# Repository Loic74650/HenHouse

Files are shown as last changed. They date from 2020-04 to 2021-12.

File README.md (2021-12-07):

<h2>HenHouse V2.0</h2>
<h3>solar powered smart and automated hen house system with LoRaWan connectivity</h3><br />

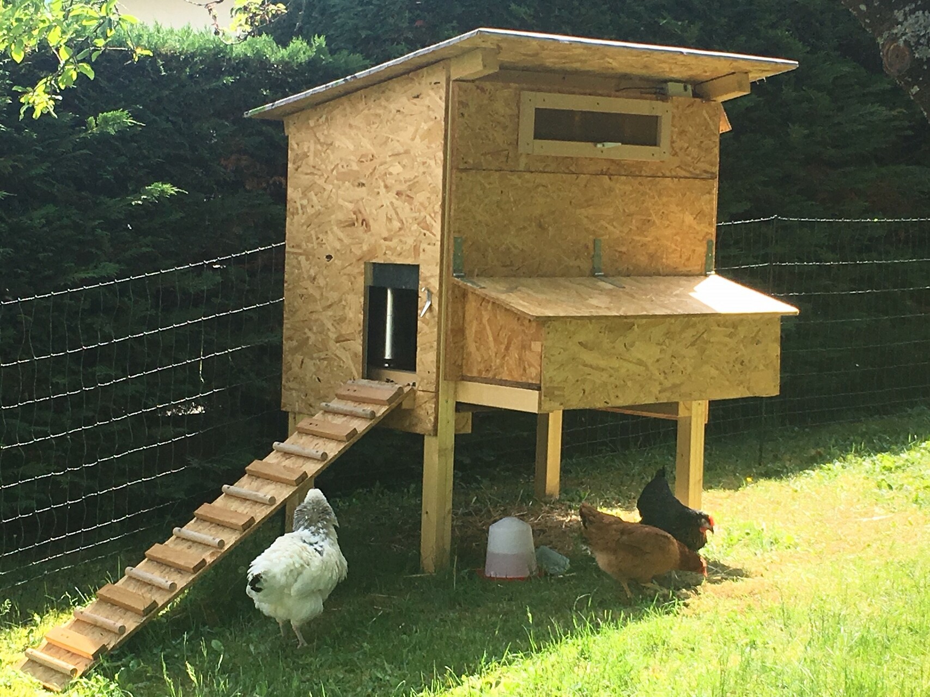
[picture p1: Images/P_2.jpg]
 <br /><br />

<h4>Key features</h4>
<li>Runs on an Adafruit Feather M0 board (ATSAMD21G18 ARM Cortex M0 processor, clocked at 48 MHz and at 3.3V logic) equiped with a LoRa Radio Module</li>
<li>LoraWan connectivity to TTN network based on LMIC fully compliant library</li>
<li>Entrance guillotine-style door is motorized. Two reed end-switches detect the door open/close positions</li>
<li>UP/DOWN interface buttons to manually force door opening/closing</li>
<li>Door automatically opens/closes at sunrise and sunset (as a function of an ambient light threshold, measured via the solar panel voltage output)</li>
<li>When door is moving, a buzzer makes intermitent beeps in order to let the chiken know it is bedtime</li>
<li>Measures the individual temperature of 4 separate nesting boxes (aim is to detect when a new egg was layed) + computes an average</li>
<li>Runs on a 3.7V 4400mAh Lithium Ion Battery Pack and a 6V, 1W solar panel</li>
<li>Goes to deep sleep until UP/DOWN buttons are pressed. 80µA Current consumption in deep sleep mode. </li>
<li>broadcasts over LoraWan every three minutes the systems’ metrics (temperatures, ambient light level, door position, battery level and charging status), received by home automation system in JSON format via MQTT broker</li><br /><br />

In order to broadcast data to the TTN network, you need to register an account as well as the Feather board. <a title="https://learn.adafruit.com/the-things-network-for-feather?view=all" href="https://learn.adafruit.com/the-things-network-for-feather?view=all">Detailed instructions here</a>.<br /><br />

<h4>Hardware</h4>
<li>x1 <a title="https://learn.adafruit.com/adafruit-feather-m0-radio-with-lora-radio-module/downloads" href="https://learn.adafruit.com/adafruit-feather-m0-radio-with-lora-radio-module/downloads">Adafruit Feather M0 LoRa Radio (RFM9x)</a></li>
<li>x1 <a title="https://www.adafruit.com/product/390" href="https://www.adafruit.com/product/390">Solar Lithium Ion/Polymer charger</a></li>
<li>x1 <a title="https://www.sparkfun.com/products/14451" href="https://www.sparkfun.com/products/14451">TB6612FNG</a> motor driver</li>
<li>x1 <a title="https://www.adafruit.com/product/3809" href="https://www.adafruit.com/product/3809">6V 1W Solar Panel</a></li>
<li>x1 <a title="https://www.adafruit.com/product/354" href="https://www.adafruit.com/product/354">Lithium Ion Battery Pack - 3.7V 4400mAh </a></li>
<li>x2 <a title="https://www.adafruit.com/product/375" href="https://www.adafruit.com/product/375">magnetic contact switch (door sensors) </a></li>
<li>x1 <a title="https://fr.banggood.com/DC-3V-6V-DC-1120-Gear-Motor-TT-Motor-for-Arduino-Smart-Car-Robot-DIY-p-1260117.html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" href="https://fr.banggood.com/DC-3V-6V-DC-1120-Gear-Motor-TT-Motor-for-Arduino-Smart-Car-Robot-DIY-p-1260117.html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">motorreductor </a></li>
<li>x1 <a title="https://www.banggood.com/DC-2V-24V-To-5V-28V-2A-Step-Up-Boost-Converter-Power-Supply-Module-Adjustable-Regulator-Board-p-1566600.html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" href="https://www.banggood.com/DC-2V-24V-To-5V-28V-2A-Step-Up-Boost-Converter-Power-Supply-Module-Adjustable-Regulator-Board-p-1566600.html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">DC-DC converter 5V output</a></li>

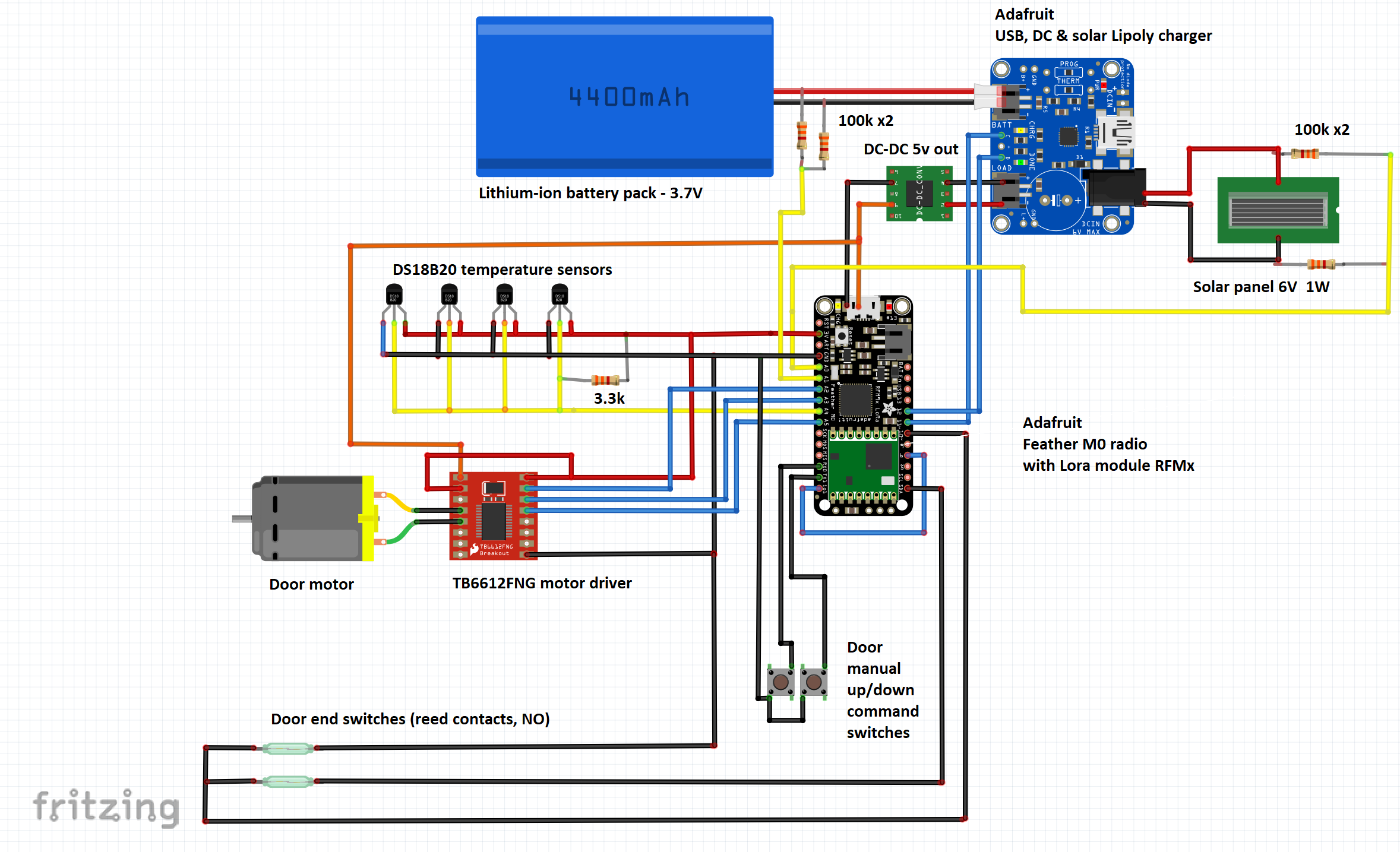
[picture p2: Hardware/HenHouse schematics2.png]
Schematics
 <br /><br />
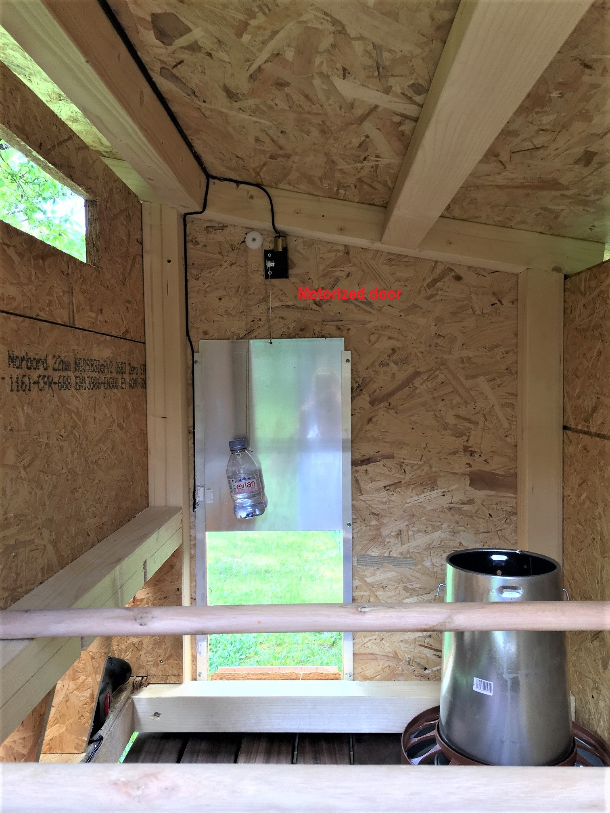
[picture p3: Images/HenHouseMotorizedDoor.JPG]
 <br /><br />
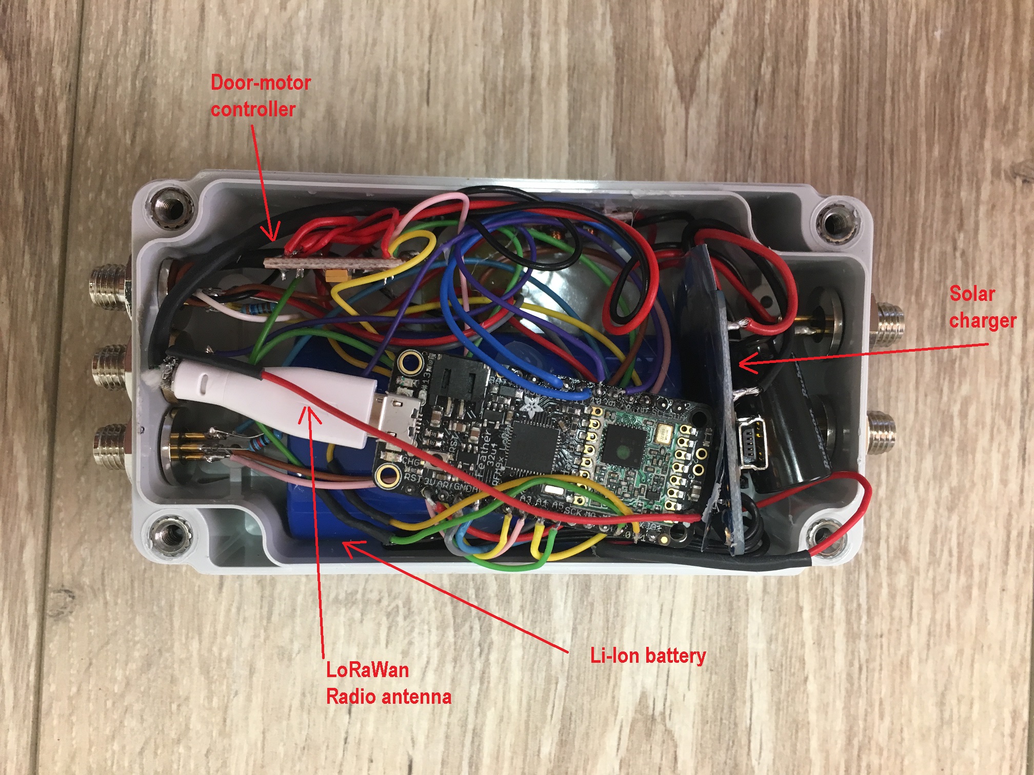
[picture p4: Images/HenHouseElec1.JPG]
 <br /><br />
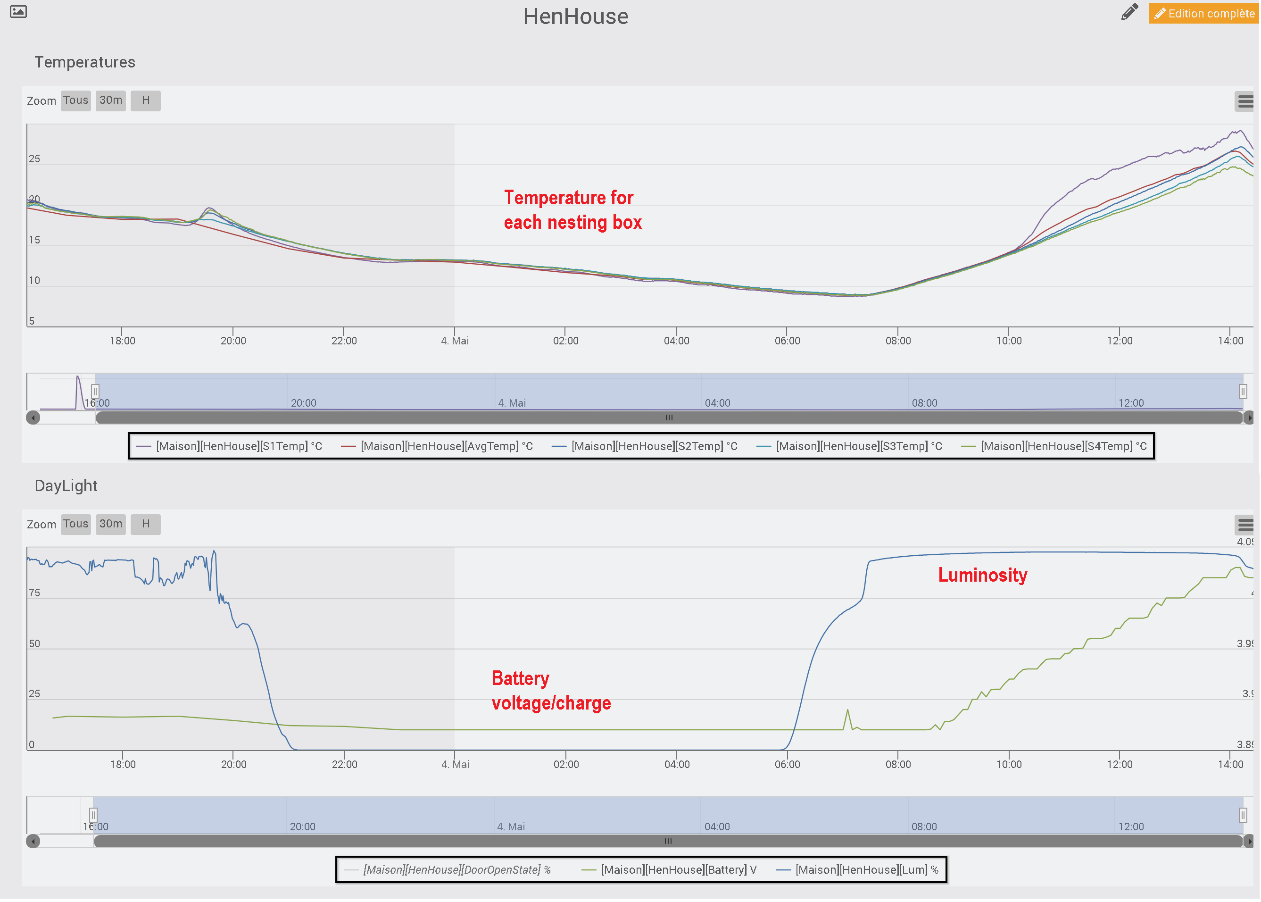
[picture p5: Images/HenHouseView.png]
 <br /><br />

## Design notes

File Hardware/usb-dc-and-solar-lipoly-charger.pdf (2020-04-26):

# USB, DC & Solar Lipoly Charger

Created by lady ada

Last updated on 2018-08-22 03:31:26 PM UTC

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
## Guide Contents

## Guide Contents Overview FAQ

Is this a MPPT tracker?
Why didn't you make this an MPPT?
BUT I HEARD THAT MPPT IS THE BEST!!
OK so how does it work?
What solar panels can I use?
Can I charge with a solar panel on my windowsill?

## Solar Charger Preparation

Installing the Capacitor

## Solar Panel Preparation

Splice or Adapt?

## Voltaic Panels with 1.3mm Connectors Other 6V Solar Panels

Method 1

## If You Have a Pre-2013 Solar Charger Using the Charger

Solar Charging
USB & DC Charging
Indicator LEDs

## Load Sharing

Temperature Monitoring
Adjusting the Max Charge Current

## Adding External LEDs Design Notes

Is this a Max Power Point Tracker (MPPT)? Why a special solar charger?
Solar Optimization!

## Downloads Files Schematic & Fabrication Print

© Adafruit Industries | https://learn.adafruit.com/usb-dc-and-solar-lipoly-charger | Page 2 of 29

## Overview

Make your projects to go green this summer with our specialized USB/Solar Lithium Ion Polymer Battery charger! This charger is a very unique design, perfect for outdoor projects, or DIY iPod chargers. We've spent over a year testing and tinkering with this charger to come up with a plug and play solution to charging batteries with the sun and we're really pleased with what we ended up with.

Easy to use! Pick up any of our many 3.7V/4.2V LiIon batteries (http://www.adafruit.com/category/44) (https://adafru.it/aN5), and a 6V solar
panel (https://adafru.it/aN6). Plug the battery into the BATT port using a 2-pin JST cable and the solar (http://www.adafruit.com/category/67) panel into the DC jack. Put the solar panel outside (and keep the battery out of the sun, it needs to be kept shaded!) to start charging. You can power another project like a Mintyboost at the same time by connecting to the LOAD output port

3.7V/4.2V Lithium Ion or Lithium Polymer battery charger
Charge with 5-6V DC, USB or 6V solar panel!
Too dark out? Use a USB mini-B cable (http://www.adafruit.com/products/260) (http://adafru.it/260) or a 5V DC adapter (http://www.adafruit.com/products/276) (http://adafru.it/276) Automatic charging current tracking for high efficiency use of any wattage solar panel
Use any 6V solar panel (6V seems to work best, 5.5V may work, 5V does not work)
Three color indicator LEDs - Power good, Charging and Done
Low Battery Indicator (fixed at 3.1V) with LED output on (labeled CHRG)
Set for 500mA max charge rate, can be adjusted from 50mA up to 1A by soldering in a resistor
Will always draw the most current possible from a solar cell - up to the max charge rate!
Smart load sharing automatically uses the input power when available, to keep battery from constantly charging/discharging
Temperature monitoring of battery by soldering in a 10K NTC thermistor(http://adafru.it/372) (http://www.adafruit.com/products/372) (not included) -suggested for outdoor projects where the battery may get hot (50°C) or cold (0°C).
© Adafruit Industries | https://learn.adafruit.com/usb-dc-and-solar-lipoly-charger | Page 3 of 29

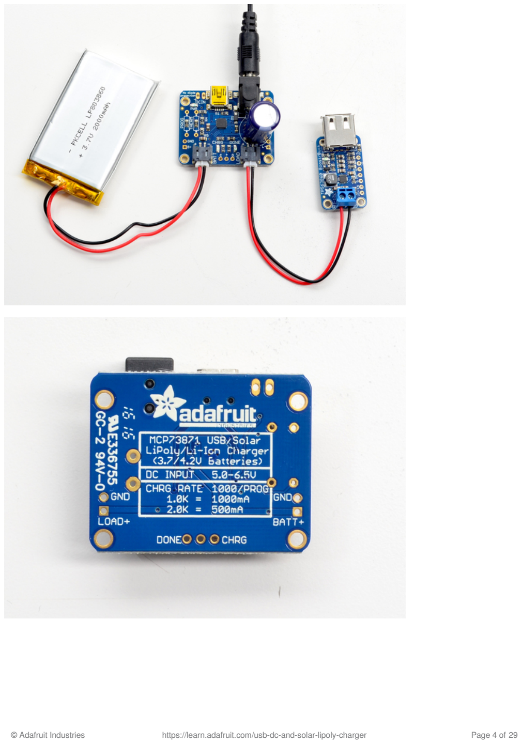
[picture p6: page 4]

© Adafruit Industries | https://learn.adafruit.com/usb-dc-and-solar-lipoly-charger | Page 4 of 29

## FAQ

Is this a MPPT tracker?
This is not a true MPPT tracker, for information on why we did not design it as a true MPPT, read our design notes! (http://learn.adafruit.com/usb-dc-and-solar-lipoly-charger/design-notes)

Why didn't you make this an MPPT?
For low power solar charging of lithium ion's, its not necessarily a better way to charge.For information on why we did not design it as a true MPPT, read our design notes! (http://learn.adafruit.com/usb-dc-and-solar-lipoly-charger/design-notes)

BUT I HEARD THAT MPPT IS THE BEST!!
For large multi-watt solar arrays that are charging lead acid batteries, you will want to get an MPPT charger. For small cells, its not necessarily more efficient. For information on why we did not design it as a true MPPT, read our design notes! (http://learn.adafruit.com/usb-dc-and-solar-lipoly-charger/design-notes)

OK so how does it work?
Good question! For information on how this charger works, read our design notes! (http://learn.adafruit.com/usb-dc-and-solar-lipoly-charger/design-notes)

What solar panels can I use?
Use any rigid, flexible, monocrystal, polycrystal, etc panels with 6V rating (12 'cells') for the best performance

We've tried 5V panels and they don't work. 5.5V panels sometimes work, 6V is really the best!

Can I charge with a solar panel on my windowsill?
The charger will draw as much current as possible, but the efficiency of the panel will be much lower. Solar panels must not have any glass or shade to work efficiently, they must be outside, pointed as best as possible directly at the sun!
© Adafruit Industries | https://learn.adafruit.com/usb-dc-and-solar-lipoly-charger | Page 5 of 29

## Solar Charger Preparation

## Installing the Capacitor

The first thing to do before starting to charge with a solar panel is to install the large filtering capacitor. This capacitor is necessary to stabilize the panel a little, and since we're going to charge with a lot of current, the capacitor needs to be pretty big. There is a spot on the PCB for the capacitor, you can of course install it directly there by soldering the wires of the capacitor into the pads.

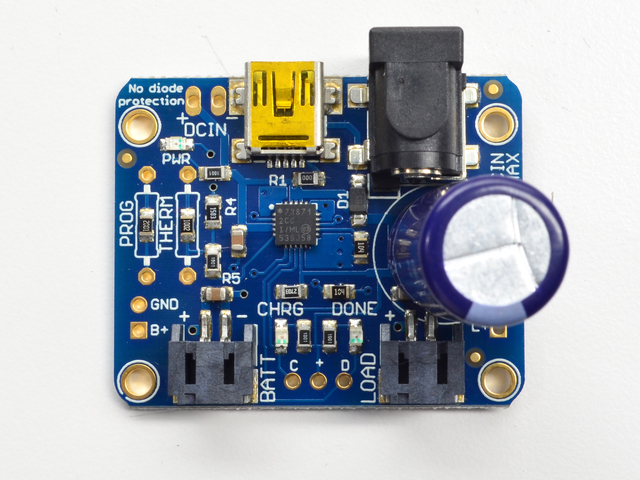
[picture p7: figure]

If you're low on space, you can solder wires to the capacitor and then install it a little farther away. Just remember to use heatshrink to keep the capacitor legs from shorting. If you want you can bend the capacitor over a bit as well, but dont have it touch the hot charging chip (the black square in the middle of the PCB)!

Next you will have to connect up your solar panel. Panels sometimes come 'bare' (no wires), with just wires, or with a connector of some sort. You may need to splice a connector onto the panel to match the 5.5/2.1mm (or 4mm on older charger) DC jack on the adapter.

Make sure to check the polarity of the capacitor, make sure the positive lead of the capacitor goes into the pad marked +!

© Adafruit Industries | https://learn.adafruit.com/usb-dc-and-solar-lipoly-charger | Page 6 of 29

## Solar Panel Preparation

## Splice or Adapt?

The first verison of the solar charger came with a 4mm DC barrel jack on it. On older versions (4mm) it would come with a converter cable.

If you have a newer v2 charger (June 2013+), connect a2.1mm Terminal Block Adapter (http://www.adafruit.com/products/369) (http://adafru.it/369) onto the panel using basic wires, or a 1.3mm to 2.1mm adapter cable (https://www.adafruit.com/products/2788) (http://adafru.it/2788) then plug that into the 2.1mm adapter. This is the fastest method

If you have an older v1 charger, you can use the terminal block method above OR cut the adapter cable in half and splice the 4mm connector onto the panel. The panel will plug right into the board but its more work.

## Voltaic Panels with 1.3mm Connectors

Grab one of our adapter cables, it will let you plug in the solar panel directly (https://www.adafruit.com/products/2788) (http://adafru.it/2788)

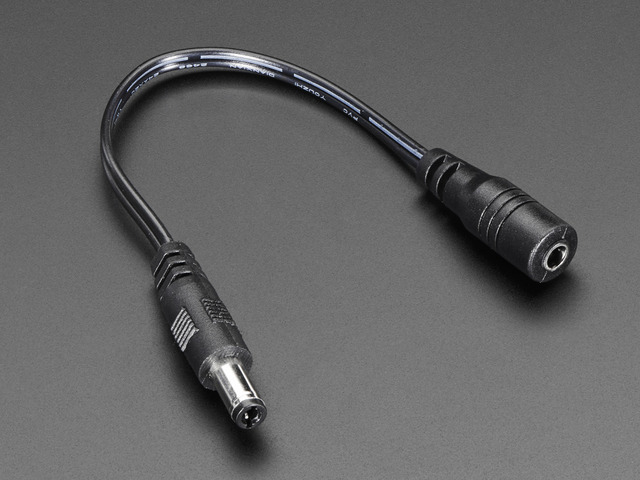
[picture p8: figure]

## Other 6V Solar Panels

If you have a panel with something other than 2.1mm or 1.3mm connector, you'll need to remove any existing connector. Cut off whatever connector is on

© Adafruit Industries | https://learn.adafruit.com/usb-dc-and-solar-lipoly-charger | Page 7 of 29

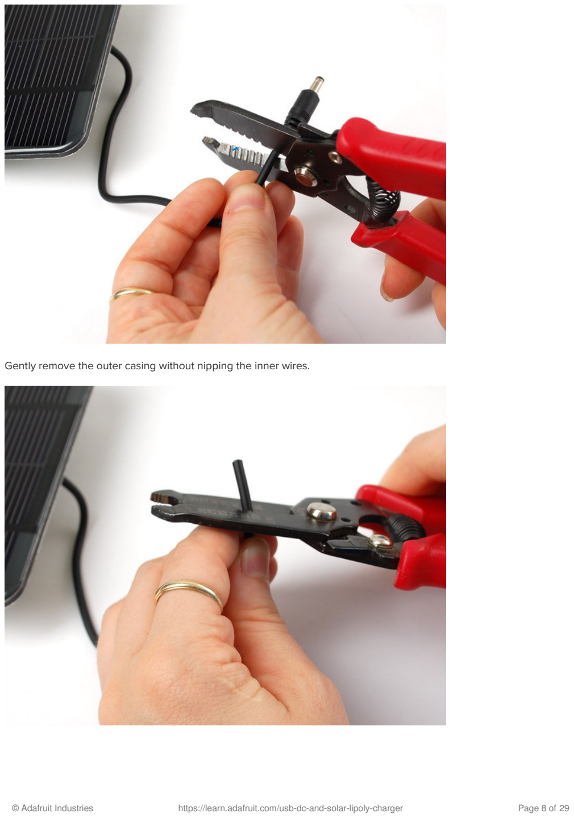
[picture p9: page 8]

Gently remove the outer casing without nipping the inner wires.

© Adafruit Industries | https://learn.adafruit.com/usb-dc-and-solar-lipoly-charger | Page 8 of 29

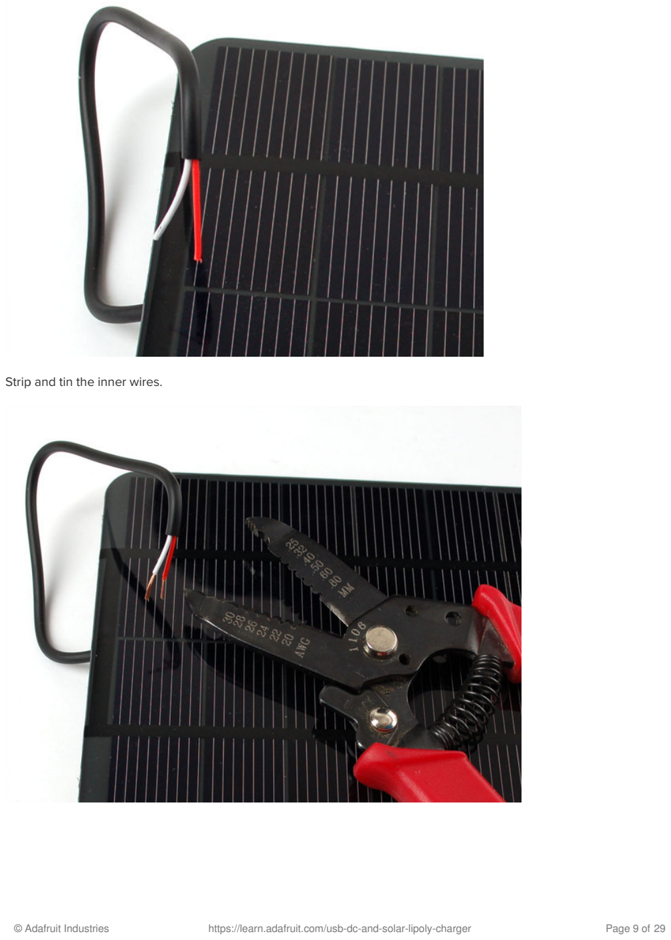
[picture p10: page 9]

Strip and tin the inner wires.

© Adafruit Industries | https://learn.adafruit.com/usb-dc-and-solar-lipoly-charger | Page 9 of 29

## Method 1

For this you'll need a 2.1mm Terminal Block Adapter (http://www.adafruit.com/products/369) (http://adafru.it/369) but its really simple. Just open up the screw terminals, slide the red wire into the + hole and the black wire into the - hole and retighten! Now you can just plug it directly into the charger (or adapter cable).

## If You Have a Pre-2013 Solar Charger

© Adafruit Industries | https://learn.adafruit.com/usb-dc-and-solar-lipoly-charger | Page 10 of 29

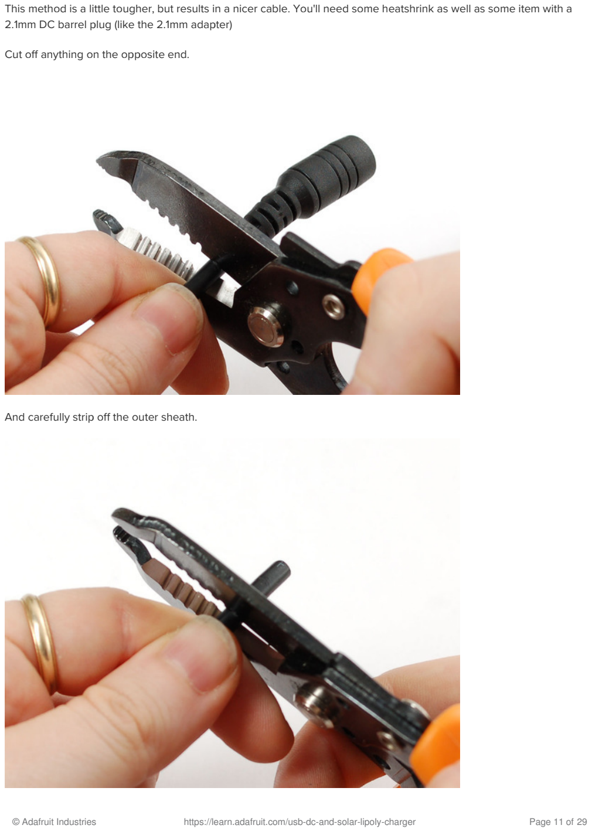
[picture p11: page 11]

This method is a little tougher, but results in a nicer cable. You'll need some heatshrink as well as some item with a 2.1mm DC barrel plug (like the 2.1mm adapter)

Cut off anything on the opposite end.

And carefully strip off the outer sheath.

© Adafruit Industries | https://learn.adafruit.com/usb-dc-and-solar-lipoly-charger | Page 11 of 29

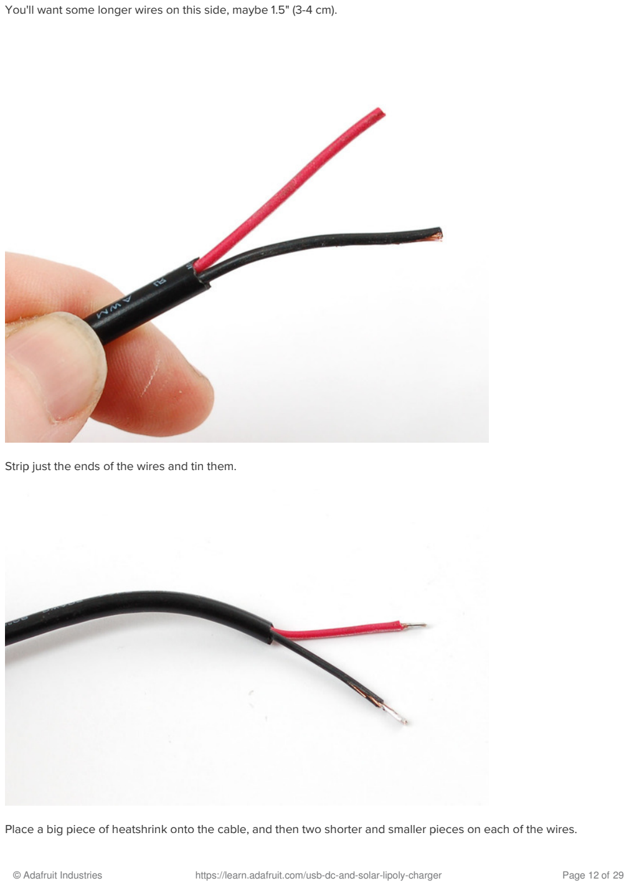
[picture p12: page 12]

You'll want some longer wires on this side, maybe 1.5" (3-4 cm).

Strip just the ends of the wires and tin them.

Place a big piece of heatshrink onto the cable, and then two shorter and smaller pieces on each of the wires.

© Adafruit Industries | https://learn.adafruit.com/usb-dc-and-solar-lipoly-charger | Page 12 of 29

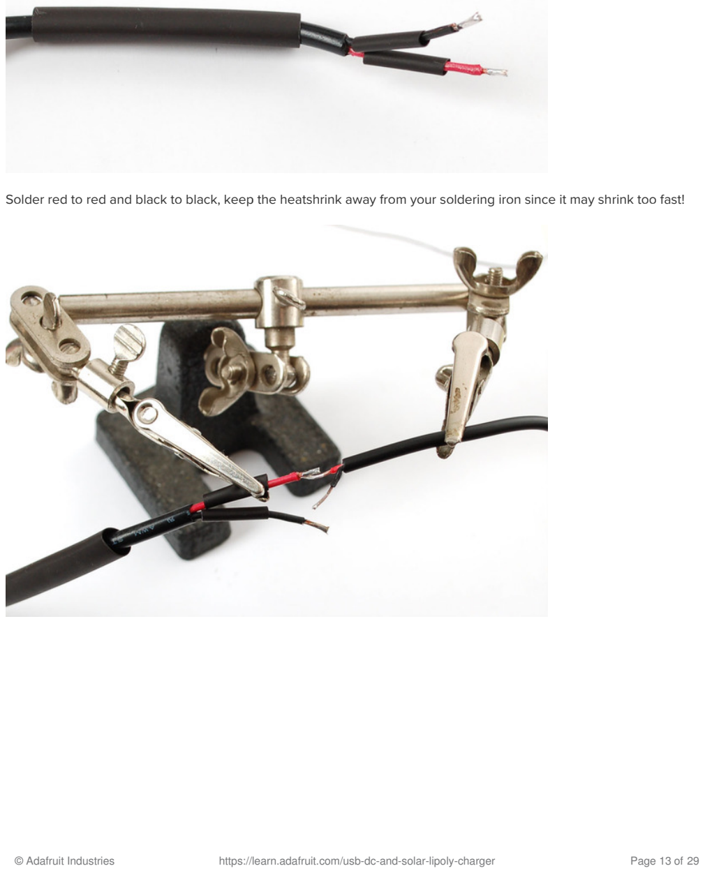
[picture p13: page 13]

Solder red to red and black to black, keep the heatshrink away from your soldering iron since it may shrink too fast!

© Adafruit Industries | https://learn.adafruit.com/usb-dc-and-solar-lipoly-charger | Page 13 of 29

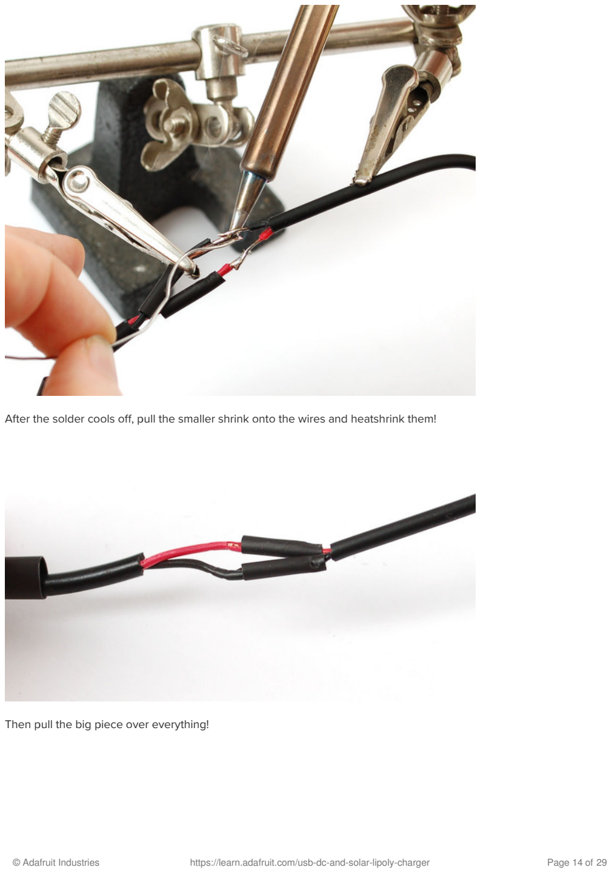
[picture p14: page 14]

After the solder cools off, pull the smaller shrink onto the wires and heatshrink them!

Then pull the big piece over everything!

© Adafruit Industries | https://learn.adafruit.com/usb-dc-and-solar-lipoly-charger | Page 14 of 29

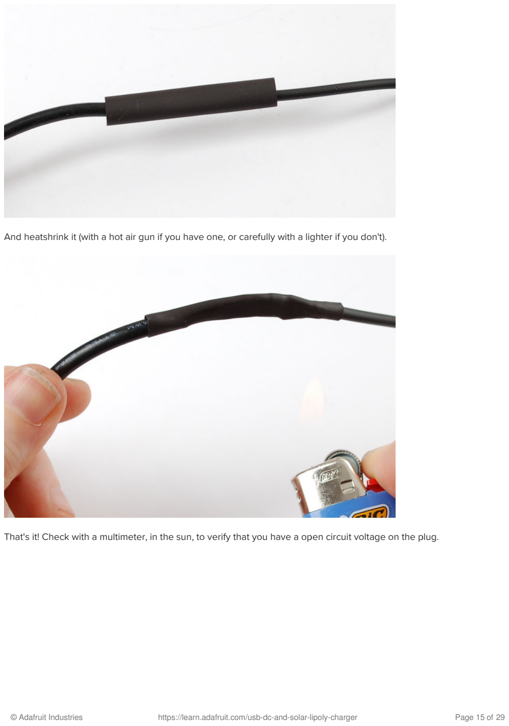
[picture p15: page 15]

And heatshrink it (with a hot air gun if you have one, or carefully with a lighter if you don't).

That's it! Check with a multimeter, in the sun, to verify that you have a open circuit voltage on the plug.

© Adafruit Industries | https://learn.adafruit.com/usb-dc-and-solar-lipoly-charger | Page 15 of 29

© Adafruit Industries | https://learn.adafruit.com/usb-dc-and-solar-lipoly-charger | Page 16 of 29

## Using the Charger

## Solar Charging

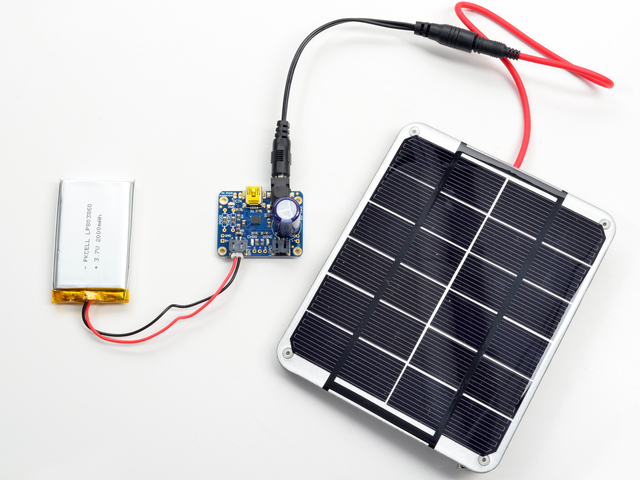
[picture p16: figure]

Solar charging is easy, don't forget to prepare your solar panel and solder in the electrolytic capacitor beforehand! (https://adafru.it/aN8) (http://learn.adafruit.com/usb-dc-and-solar-lipoly-charger/solar-charger-preparation)

Once you've done that, you can simply plug in the solar panel into the DC jack - look for the PWR GOOD LED to indicate that the solar panel is providing power and then plug the battery into the BATT slot in the left. Use only 3.7V/4.2V lithium ion/polymer batteries.

We have a tutorial about the batteries in case you have some questions about how to use them.(https://adafru.it/aN9) (http://learn.adafruit.com/li-ion-and-lipoly-batteries)

When the CHRG charging light is lit, the battery is being charged. Make sure to have the panel facing direct sunlight not shaded and not behind any glass or plastic! when the battery is full, you'll see the greenDONE LED light up.

## USB & DC Charging

Of course, sometimes is just really dark out and you can't solar charger, so there's a USB port on the board as well. Use any mini-B cable to plug in and charge.

If there is something connected to the DC jack, it will mechanically disconnect the mini USB connector so be sure to unplug the solar panel when USB charging

© Adafruit Industries | https://learn.adafruit.com/usb-dc-and-solar-lipoly-charger | Page 17 of 29

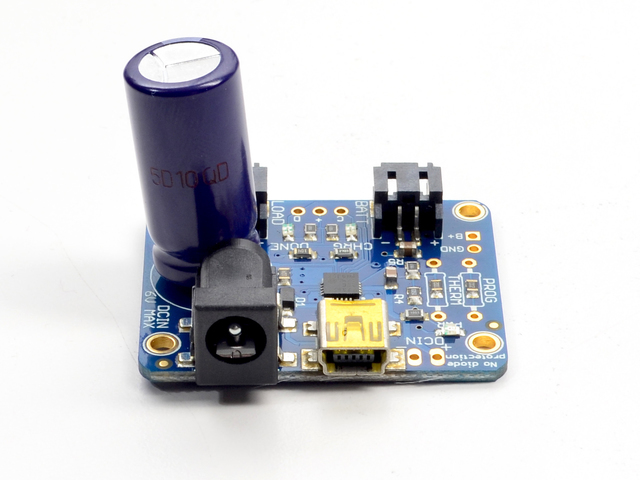
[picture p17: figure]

You can also connect a DC wall plug adapter directly into the jack, just make sure its a 5.5mm/2.1mm inner diameter connector, which is very common!

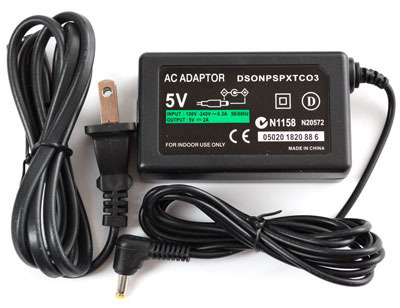
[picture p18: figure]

If you need the DC power for something else, you can also connect to the DC input via the 0.1" breakout. While you can feed power into the breakout pins as well, it's not polarity protected so make sure you use a schottky diode or just be really careful.

## Indicator LEDs

There are three status LEDs on the charger, which you'll find very handy!

The red PWR LED indicates that there is good power connected to the charger. If this LED is not lit, something is wrong with the power supply

© Adafruit Industries | https://learn.adafruit.com/usb-dc-and-solar-lipoly-charger | Page 18 of 29

The orange CHRG LED indicates current charging status. When this LED is lit, the charger is working to charge up a battery! It also acts as a low battery indicator (fixed at 3.1V) when no power is connected. So, if you don't have USB/Solar wired up, when the battery voltage drops below 3.1V, the orange LED will come on.

The green DONE LED is pretty easy to understand as well - when it's lit the battery is charged up! Very handy for when you want to know that everything is done.

If you need to connect larger LEDs or a microcontroller up to these status pins, you can us the STATUS 0.1" breakout on the bottom edge of the PCB. The pins are open drain, so they will short to ground when 'active' and float when 'inactive' - you'll want to use a pullup resistor if you need a digital signal or connect LEDs just like shown below on the schematic, if you want bigger lights.

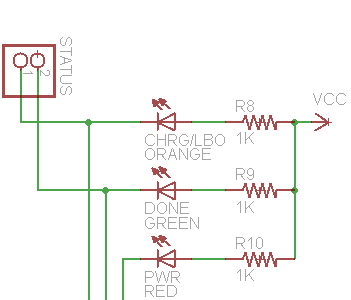
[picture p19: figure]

## Load Sharing

The MCP73871 chip in the usb/solar charger has a very nifty feature called 'load sharing.' Say you have an every day lipoly charger and you want to use the battery while its charging. To do this, you might connect the project directly to the battery output. This means, however, that the charger is both charging a battery and driving your project at the same time. The charger is working extra hard and the battery is being charged and discharged constantly.

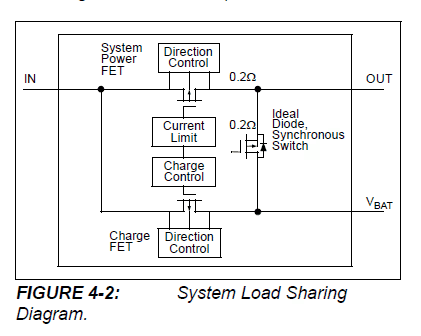
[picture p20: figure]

As an improvement, this design has a pass transistor inside the chip, connected to the output load from the input voltage, so that you dont lose efficiency from charging/discharging the battery. When the USB/Solar charger is

© Adafruit Industries | https://learn.adafruit.com/usb-dc-and-solar-lipoly-charger | Page 19 of 29

powered from a USB port or panel, the load current goes directly from the input voltage to the output. If the current required is higher than what the panel or USB port can provide, the current is supplemented by the lipo battery, up to 1.8A

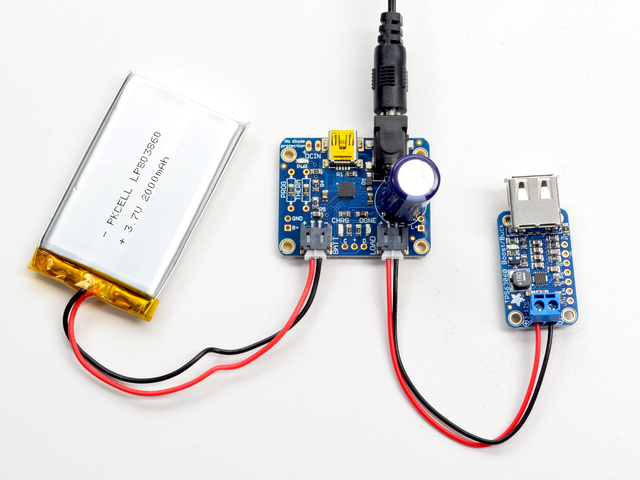
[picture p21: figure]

This is all managed at the same time as the solar current maximization. Simply plug in the lipoly battery on the left into the BATT port and connect your project up thru the LOAD port on the right.

## Temperature Monitoring

If you plan to have your project outside or unattended, we suggest adding temperature sensing to keep the charger from overheating the battery or attempting to charge when the battery is too hot or cold.

The smart load sharing means that the LOAD output can be as high as 6VDC if in direct sun because it will draw current directly from the 6V panel instead of from the battery. If using this with an electronic project, make sure it is OK for up to 6VDC input or use a low-dropout-regulator (LDO) to regulate the voltage down.

© Adafruit Industries | https://learn.adafruit.com/usb-dc-and-solar-lipoly-charger | Page 20 of 29

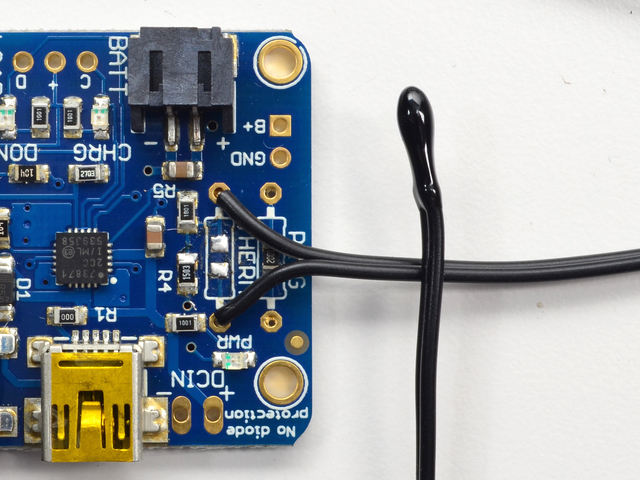
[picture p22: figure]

Simply remove the 10K surface mount resistor from the THERM pads (or cut the trace going to it), and solder in a 10K NTC thermistor (http://adafru.it/372). Test out the system by trying to charge while you place the thermistor in a freezer (http://www.adafruit.com/products/372) or against some ice, as well as in a cup of > 50°C hot water. The charger should stop charging the battery. Once you are sure it is working, attach the sensing element (the epoxy bulb in this case) so it is resting against the battery.

## Adjusting the Max Charge Current

The USB/Solar charger comes with a preset rate of 500mA which will work great for USB ports, USB wall adapters and solar panels up to 3 Watts. If you have a project that uses a larger panel, or perhaps some other sort of setup, you can easily adjust the current by soldering a resistor into the PROG pads.

© Adafruit Industries | https://learn.adafruit.com/usb-dc-and-solar-lipoly-charger | Page 21 of 29

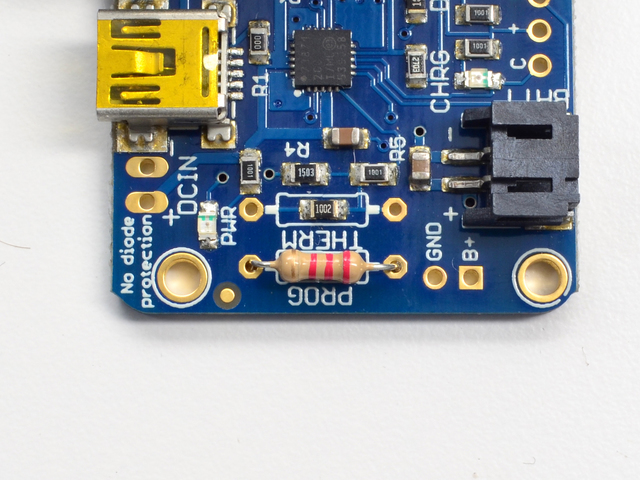
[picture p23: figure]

The current is set by 1000/RPROG Amps, where RPROG is the resistance. So for 2 Kohms, that would make it 1000/2000 = 0.5 A = 500 mA. If you want 1A, you would use a 1K ohm resistor. If you want to increase the current, you need to decrease the resistance, so you can just solder over the existing 2K. So for example, soldering another 2K resistor into RPROG will give you 1K total resistance and 1000 mA current draw. See above for a 2.2K resistor soldered for about 950mA of max current draw. If you want to set the max current draw lower, you'll need to remove the 2K resistor.

## Adding External LEDs

If you are placing the charger in a box, you may want to have external LEDs for indicating charge state. This is easy! Simply use any 3mm, 5mm or 10mm LEDs you wish and 1K resistors and wire them like so:

© Adafruit Industries | https://learn.adafruit.com/usb-dc-and-solar-lipoly-charger | Page 22 of 29

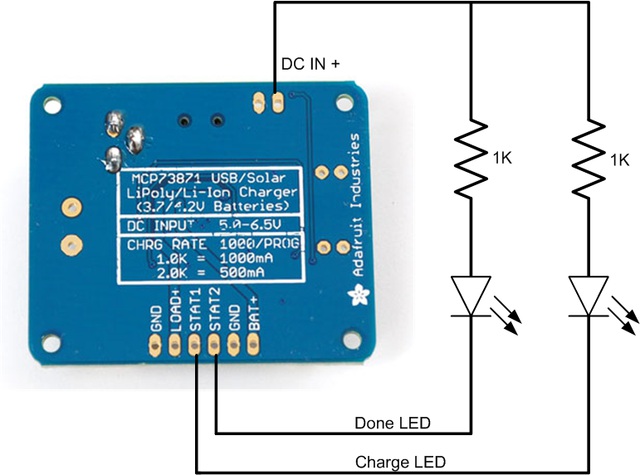
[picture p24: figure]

© Adafruit Industries | https://learn.adafruit.com/usb-dc-and-solar-lipoly-charger | Page 23 of 29

## Design Notes

## Is this a Max Power Point Tracker (MPPT)?

This design is not a 'true' MPPT, and we did that for a reason! Max power point trackers work by 'tracking' the voltage and current curve of a solar panel so that the total Power (Voltage * Current) is maximized. This means that as the light changes, the voltage and current must be carefully tracked. In general, the way controllers perform MPPT is to have a DC/DC converter - that's because to have the best power conversion you'll want DC/DC not linear converters (that lose any excess voltage as heat). For example, say you want to charge a 6V lead acid battery and you have a 12V (approx) panel. The voltage will range between 9V and 14V depending on current draw and visible light. The buck converter will do its best to keep the current draw so that the total power available at the output is maximized.

This diagram from Linear (https://adafru.it/CbQ) is really good at describing how it works:

The Green lines show the I-V curve of the panel for a given light condition. As the light increases the voltages stay sort of the same but the amount of current you can draw goes up! If you can keep the DC/DC converter operating on the red line, that's the maximum power.

However, there are some side effects to using a MPPT design.

First is that DC/DC converters are expensive, and adding a DC/DC converter to a LiPo charger chip increases the cost by 2x. For small panels, if the MPPT increases the efficiency by 30% but you can double the panel size for the same price increase, it might be easier to just go with a larger panel.

Second is that DC/DC converters are not necessarily more efficient than a linear converter at low voltages and currents. At the voltages we're talking about, a 6V panel charging a 4V battery, the max power point will tend to be around 5V - only a volt above the battery. Considering there's a 0.5V drop with the input diode, the added inefficiency of a DC/DC converter is about equivalent to the extra voltage drop used by the linear charger. For this reason, you tend to see MPPT controllers only for multi-ampere chargers for big lead acid batteries and really big panels.

So the upshot is...

If your panel voltage is ~1V above your battery charging voltage, your current draw is under an Ampere, and you

© Adafruit Industries | https://learn.adafruit.com/usb-dc-and-solar-lipoly-charger | Page 24 of 29

control the current draw to keep the voltage steady at around the 'max power voltage' (the red line up above), it's possible to get near-MPPT performance, without the complexity of a DC/DC converter, and without the high price. That's what the design of this charger does.

## Why a special solar charger?

We've had a lot of customers that are interested in making solar powered projects, so we wanted to make a lipo charger board that is specifically designed with Solar & USB charging in mind. We'll explain why...

Most people try to plug a solar panel directly into a lipo charger and while itsort of works, the battery takes forever to charge because the efficiency is terrible! That's because most lipo chargers are meant to plug into a USB port or wall, and are very simple in their design. USB ports supply 5V at up to 500mA and they're pretty solid - the voltage doesn't change much even at the max current draw. So when you plug a charger into a computer with a USB port, they just draw 500mA or so and happily chug away. Same goes for wall adapters. The voltage and current limits are kept steady.

Solar panels are a little different, the voltage and current vary constantly depending on sunlight available. They are unstable! That instability confuses battery chargers, which causes them to do one of two things: rapidly turn on and off as they try to draw more current from the panel than possible and/or draw much less current than they can, to keep the voltage from collapsing

Here is a diagram of a single solar cell, in various light conditions (the colored rainbow lines):

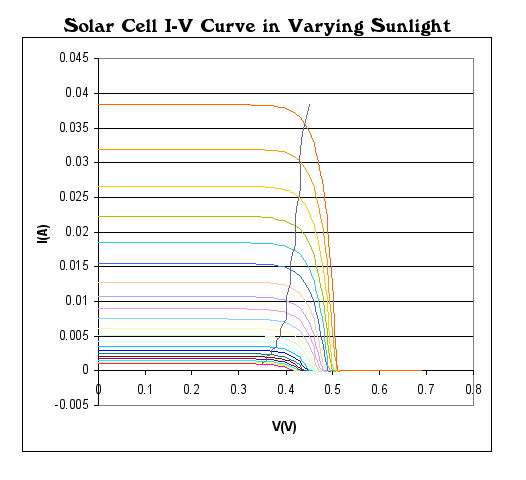
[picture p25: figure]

We find these diagrams common but a bit confusing. So we'll show how to use them. Pick the top red line (maximum light) and start at the very right of the line where it meats the horizontal scale. This is the current (I) = 0 point. We're drawing no current and the voltage of the cell is 0.5V. 0.5V is the open circuit voltage. Keep following the graph up and to the left. As the current draw increases, the voltage drops slightly until we reach the point of drawing 38mA (0.038A). At this point, the voltage is around 0.4V. Next draw a bit more current, moving to the left some more and the voltage starts collapsing.We can try to draw more current but as you can see, drawing even a tiny bit more than 38mA

© Adafruit Industries | https://learn.adafruit.com/usb-dc-and-solar-lipoly-charger | Page 25 of 29

makes the cell voltage drop to 0V. 38mA is the short circuit current

Depending on the light conditions, the amount of maximum current can range, from 38mA (red) to 32 mA (orange) down to 5mA (yellow) or even lower. Solar cells can be made larger (the short circuit current is bigger) but the voltage of the cell is fixed at 0.5V open circuit - it's just part the physics of the cell. However, you can connect a bunch of cells in series to add them up. A 6V panel has 12 cells (12 * 0.5V = 6V)

Now you can see what happens if you connect a 6V solar panel to a lipoly charger. As long as the current being drawn by the charger is less than the panel's short circuit current at that light condition, everything is peachy. The moment the light changes even a little, and the current the lipo charger wants is higher than the short circuit current, the charger becomes unstable: it will draw too much current, which will cause the voltage to collapse, which causes the charger to turn off, which reduces the current draw, which makes the panel voltage recover, which turns on the charger again, which then draws too much current, and the cycle repeats.

You can see this happen in the image from my scope below:

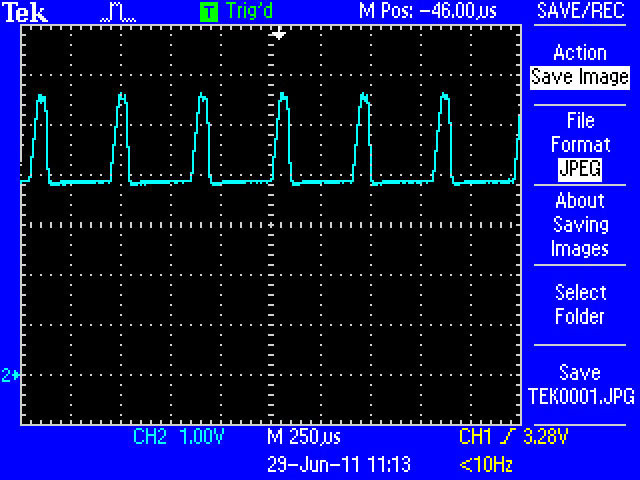
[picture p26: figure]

The scale is 1V per square, and the 0V point is one square above the bottom of the display (see the 2-> on the left) The open circuit voltage of the panel is about 6.5V, the lipo charger draws some current and quickly the panel voltage collapses. After 250 us, the charger tries again, but fails again. The lipo charger may seem to be charging because the CHRG light is on but really its doing a poor job of it!

## Solar Optimization!

OK so how do we fix this problem? The issue we have here is that the voltage collapses during high current draw. We need to find a way to keep the lipo charger from drawing too much current, and backing off when the voltage starts to droop. We looked high and low and finally found a chip that has something like this built in. The MCP73871 calls it Voltage Proportional Charge Control (VPCC) and basically, it does precisely what we want. We can set the voltage to a point just above the battery charge voltage point (say 4.5V) and then instruct the charger to draw as much current as possible. It will automatically increase/reduce the charge rate to keep the voltage higher than 4.5V!

© Adafruit Industries | https://learn.adafruit.com/usb-dc-and-solar-lipoly-charger | Page 26 of 29

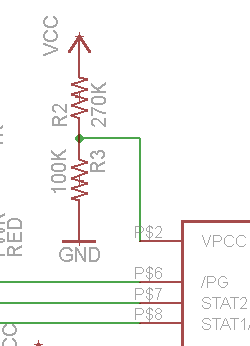
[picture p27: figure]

In this case, we set the voltage using two resistors, the voltage divider ends up stabilizing it at ~4.5V. Because the voltage collapse of a panel is really sudden, we still end up needing a little more help stabilizing the panel. We do that by adding a BFC (Big Freaking Capacitor).

This schottky diode charges a 4700uF capacitor from the panel - the diode prevents the capacitor from draining back into the panel.

© Adafruit Industries | https://learn.adafruit.com/usb-dc-and-solar-lipoly-charger | Page 27 of 29

## Downloads Files

MCP73871 datasheet (http://www.adafruit.com/datasheets/MCP73871.pdf) (https://adafru.it/aMO)
Fritzing object in Adafruit Fritzing library (https://github.com/adafruit/Fritzing-Library) (https://adafru.it/aP3)
EagleCAD Board / Layout & Schematic files on Github (https://github.com/adafruit/USB-DC-Solar-Lithium-Ion-Polymer-charger) (https://adafru.it/aMP)

## Schematic & Fabrication Print

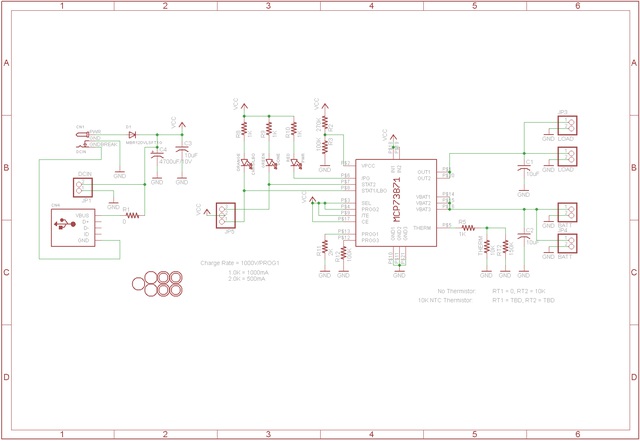
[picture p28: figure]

© Adafruit Industries | https://learn.adafruit.com/usb-dc-and-solar-lipoly-charger | Page 28 of 29

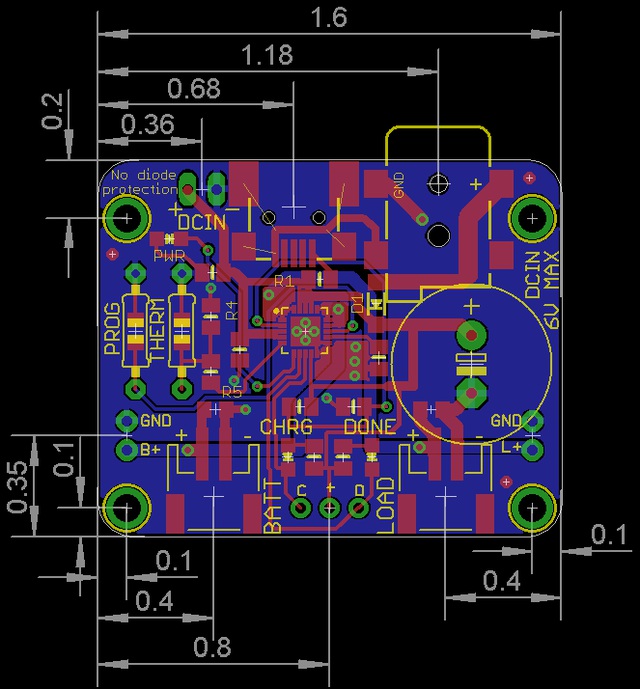
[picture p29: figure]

© Adafruit Industries | Last Updated: 2018-08-22 03:31:22 PM UTC | Page 29 of 29

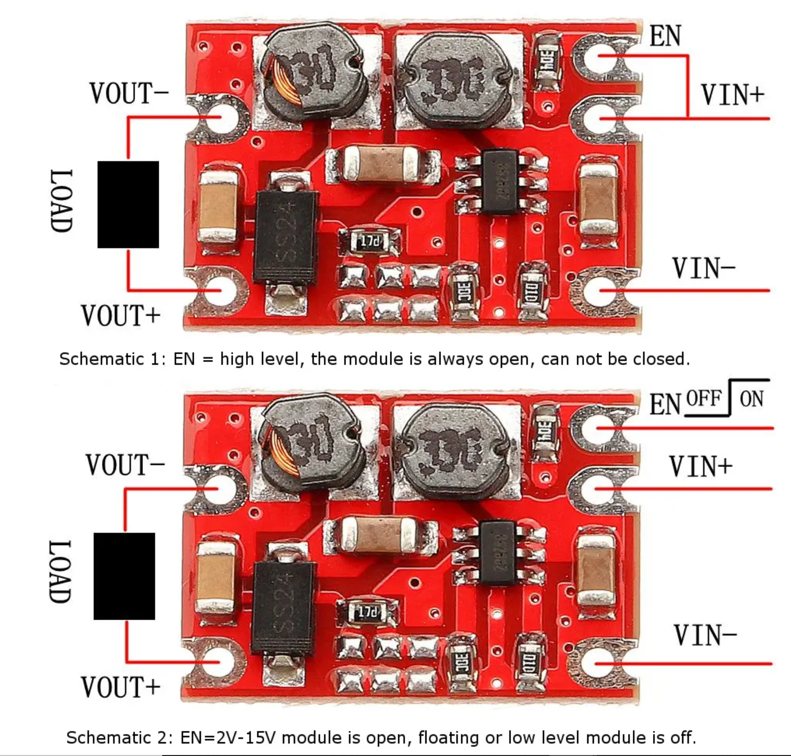
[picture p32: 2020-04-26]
Hardware/Booster.png

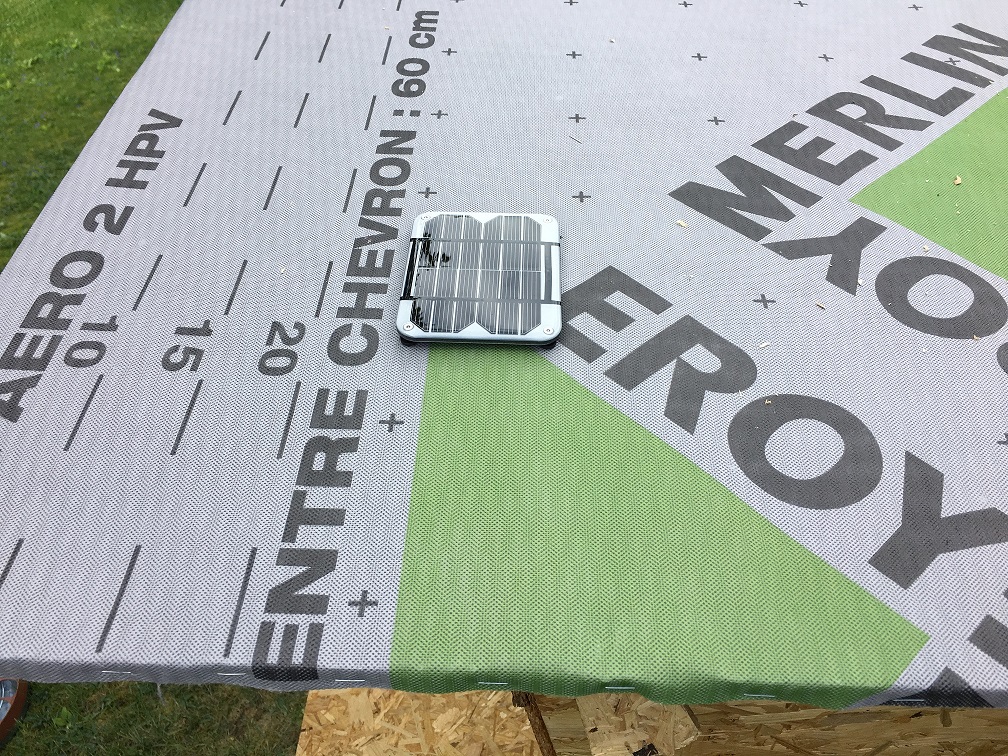
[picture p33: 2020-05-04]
Images/HenHouseSolarPanel.JPG

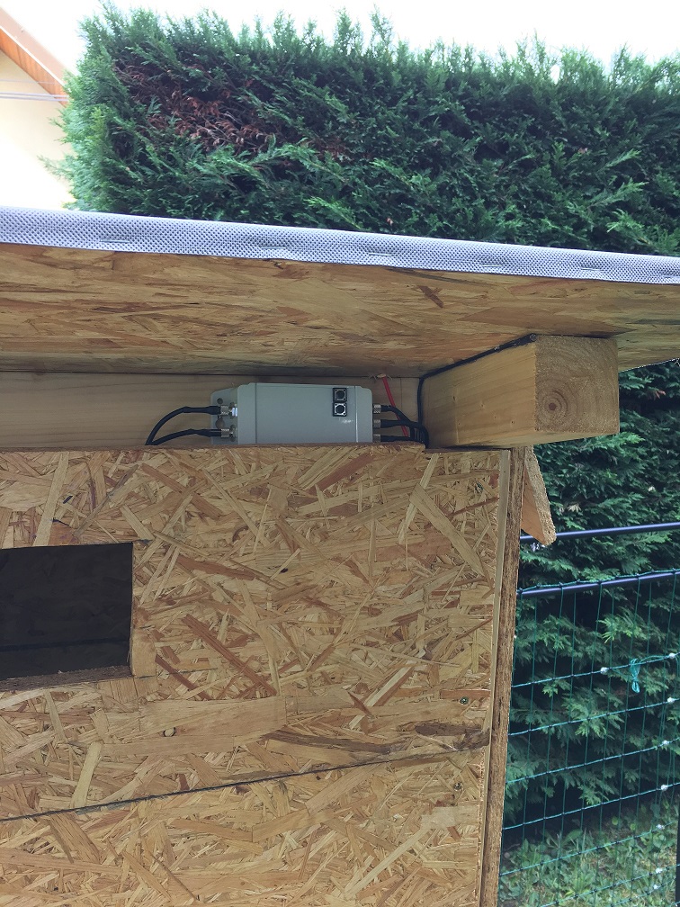
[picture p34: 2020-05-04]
Images/HenHouseElecIntegrated.JPG

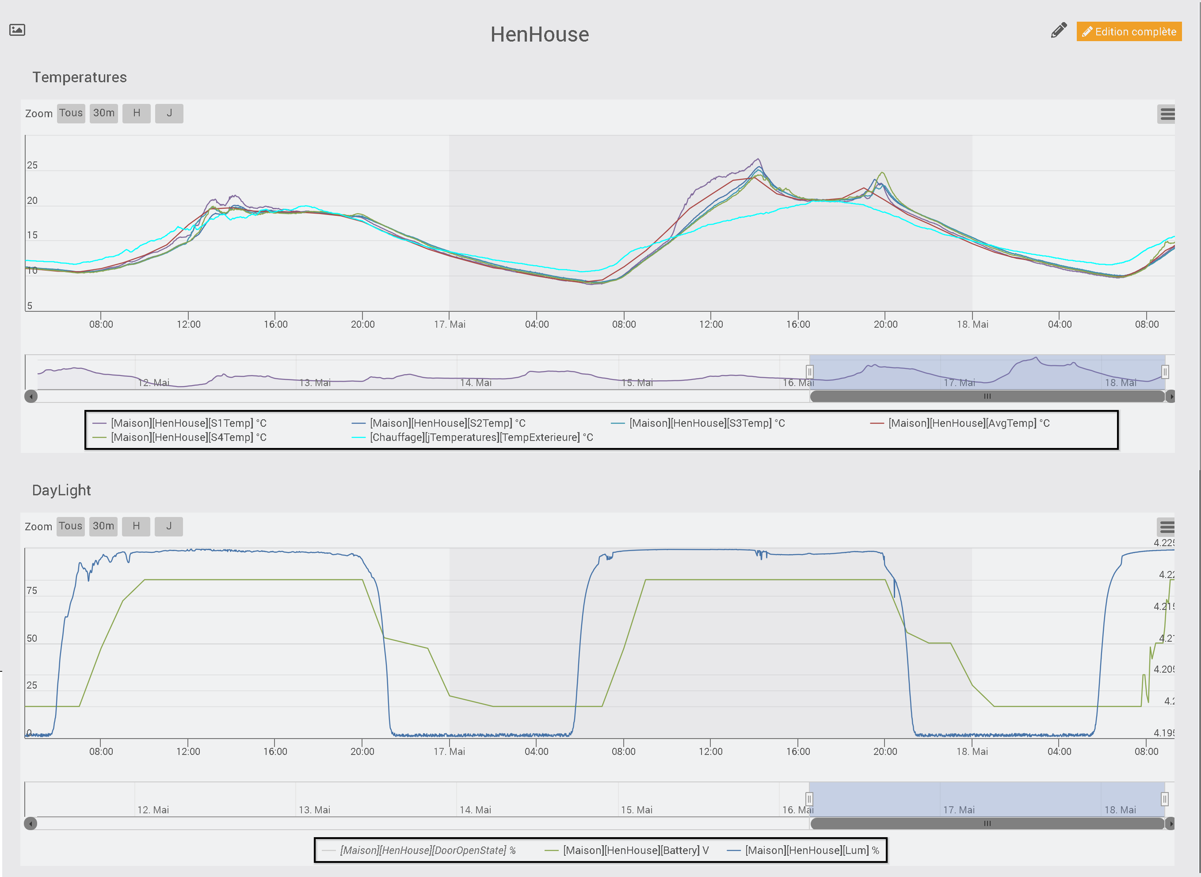
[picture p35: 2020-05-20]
Images/HenHouseView2.png

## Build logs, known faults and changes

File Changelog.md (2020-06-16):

HenHouse: change log
=======================

v0.0.3
-------

* Added a buzzer which makes intermitent beeps when door is actuated in order to let the chiken now it is bedtime
* ditched the photo-resistor as it was unable to measure accurately enough dark nights (and as a result would shut door too early for the chicken). Now using the voltage from the solar panel to decide when to open/close door

-------

* Added debug mode printing macro
* When door is manually actuated, it now stays in given state (open or close) until the next morning/evening
* Now two thresholds for the door automated open/close, one for morning and one for evening
* Updated door state machine code, now more reactive

v0.0.1
-------

* First commit

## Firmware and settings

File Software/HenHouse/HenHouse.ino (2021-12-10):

/*
  HenHouse V2.0 (c) Loic74 <loic74650@gmail.com> 2020-2021
  HenHouse solar-powered intelligent controller:
  UP/DOWN interface buttons to control Guillotine door opening/closing
  Door has endswitches to stop opening/closing as well as a timeout if endswitches were not reached in time
  Measures temperature in 4 egg-slots + an average of the 4 sensors
  Measures battery voltage as well as charging state (charging, done)
  Goes to DeepSleep until UP/DOWN buttons are pressed or until watchdog wakes it up (every 5 minutes) to broadcast measured inputs data over LoRaWan

  Visit your https://eu1.cloud.thethings.network/console/ device console
  to create an account, and obtain the session keys below which are unique to every board.

  You should then create a file called "arduino_secrets.h", save it in the project folder, and into which you will paste those unique keys in the following form:

  -------------------------------------------------------------------------------------------

  // This EUI must be in little-endian format (lsb), so least-significant-byte
  // first. When copying an EUI from ttnctl output, this means to reverse
  // the bytes. For TTN issued EUIs the last bytes should be 0xD5, 0xB3,
  // 0x70.
  static const u1_t PROGMEM APPEUI[8]={ 0x00, 0x00, 0x00, 0x00, 0x00, 0x00, 0x00, 0x00 };
  void os_getArtEui (u1_t* buf) { memcpy_P(buf, APPEUI, 8);}

  // This should also be in little endian format (lsb), see above.
  static const u1_t PROGMEM DEVEUI[8]={ 0x13, 0x05, 0x11, 0x00, 0xXX, 0xXX, 0xXX, 0xXX };
  void os_getDevEui (u1_t* buf) { memcpy_P(buf, DEVEUI, 8);}

  // This key should be in big endian format (msb) (or, since it is not really a
  // number but a block of memory, endianness does not really apply). In
  // practice, a key taken from ttnctl can be copied as-is.
  static const u1_t PROGMEM APPKEY[16] = { 0x0A, 0x60, 0xDE, 0x98, 0x1A, 0x43, 0xC8, 0x1B, 0xF2, 0xXX, 0xXX, 0xXX, 0xXX, 0xXX, 0xXX, 0xXX };
  void os_getDevKey (u1_t* buf) {  memcpy_P(buf, APPKEY, 16);}

  --------------------------------------------------------------------------------------------

***Dependencies and respective revisions used to compile this project***
  https://github.com/PaulStoffregen/OneWire (rev 2.3.4)
  https://github.com/milesburton/Arduino-Temperature-Control-Library (rev 3.7.2)
  https://github.com/bricofoy/yasm (rev 0.9.2)
  https://github.com/mcci-catena/arduino-lmic (rev 4.1.0)
  http://www.airspayce.com/mikem/arduino/RadioHead/ (rev 1.120)
  https://www.arduino.cc/libraries/ArduinoLowPower (rev 1.2.2)
*/

/*
  //TTN decoder function:

  function Decoder(bytes, port) {
  var decoded = {};

  if(port == 3)
  {
    var rawTM = bytes[0] + bytes[1] * 256;
    decoded.Mtemp = sflt162f(rawTM) * 100;

    var rawS1 = bytes[2] + bytes[3] * 256;
    decoded.S1temp = sflt162f(rawS1) * 100;

    var rawS2 = bytes[4] + bytes[5] * 256;
    decoded.S2temp = sflt162f(rawS2) * 100;

    var rawS3 = bytes[6] + bytes[7] * 256;
    decoded.S3temp = sflt162f(rawS3) * 100;

    var rawS4 = bytes[8] + bytes[9] * 256;
    decoded.S4temp = sflt162f(rawS4) * 100;

    var rawlum = bytes[10] + bytes[11] * 256;
    decoded.lum = sflt162f(rawlum) * 100;

    var rawSolum = bytes[12] + bytes[13] * 256;
    decoded.Solum = sflt162f(rawSolum) * 100;

    var rawbat = bytes[14] + bytes[15] * 256;
    decoded.bat = sflt162f(rawbat) * 100;

    var DigInt = (bytes[16] << 8) | bytes[17];

    // Decode digital inputs
    // writeBitmap(false, digitalRead(INTERLCK), digitalRead(SwDOWN), digitalRead(SwUP), digitalRead(STAT2), digitalRead(STAT1), ButtonUPPressed, ButtonDWNPressed);
    decoded.ButtonDown = (DigInt & 1) === 0?0:1;
    decoded.ButtonUp = (DigInt & 2) === 0?0:1;
    decoded.Charging = (DigInt & 4) === 0?0:1;
    decoded.DoneCharging = (DigInt & 8) === 0?0:1;
    decoded.DoorSwUp = (DigInt & 16) === 0?0:1;
    decoded.DoorSwDn = (DigInt & 32) === 0?0:1;
    decoded.DoorIntck = (DigInt & 64) === 0?0:1;
    return decoded;
  }
  else
  if(port == 4)
  {
    // Decode bytes to int
    var DoorWPos = (bytes[0] << 8) | bytes[1];
    var DoorAPos = (bytes[2] << 8) | bytes[3];

    // Decode digital inputs
    decoded.ButtonDown = (DigInt & 1) === 0?0:1;
    decoded.ButtonUp = (DigInt & 2) === 0?0:1;
    decoded.DoorSwUp = (DigInt & 16) === 0?0:1;
    decoded.DoorSwDn = (DigInt & 32) === 0?0:1;
    decoded.DoorIntck = (DigInt & 64) === 0?0:1;
    return decoded;
  }
  }

  function sflt162f(rawSflt16)
  {
  // rawSflt16 is the 2-byte number decoded from wherever;
  // it's in range 0..0xFFFF
  // bit 15 is the sign bit
  // bits 14..11 are the exponent
  // bits 10..0 are the the mantissa. Unlike IEEE format,
  // the msb is transmitted; this means that numbers
  // might not be normalized, but makes coding for
  // underflow easier.
  // As with IEEE format, negative zero is possible, so
  // we special-case that in hopes that JavaScript will
  // also cooperate.
  //
  // The result is a number in the open interval (-1.0, 1.0);
  //
  // throw away high bits for repeatability.
  rawSflt16 &= 0xFFFF;

  // special case minus zero:
  if (rawSflt16 == 0x8000)
    return -0.0;

  // extract the sign.
  var sSign = ((rawSflt16 & 0x8000) !== 0) ? -1 : 1;

  // extract the exponent
  var exp1 = (rawSflt16 >> 11) & 0xF;

  // extract the "mantissa" (the fractional part)
  var mant1 = (rawSflt16 & 0x7FF) / 2048.0;

  // convert back to a floating point number. We hope
  // that Math.pow(2, k) is handled efficiently by
  // the JS interpreter! If this is time critical code,
  // you can replace by a suitable shift and divide.
  var f_unscaled = sSign * mant1 * Math.pow(2, exp1 - 15);

  return f_unscaled;
  }*/
/************************** Configuration ***********************************/

#define SLEEP             ->comment this line to prevent µc from sleeping
//#define DOOR_PROGRESS   ->comment this line to prevent code from broadcasting door % position while opening/closing (saves Lora airtime)
#define DOOR_BUZZ         ->comment this line to prevent buzzer from going off while door opening/closing

//Buzzer PWM pin
#define BUZ 5
int Frequ = 4000;
int Duration = 300;
bool Toggle = 0;

//#define DEBUG           ->comment this line to prevent code from writing debug messages to serial port (must be commented when SLEEP is uncommented)
#include "DebugUtils.h"

// Data logging configuration.
#define LOGGING_FREQ_SECONDS   180       // Seconds to wait before a new sensor reading is logged ans sent over LoRaWan.

#include <SPI.h>
#include "OneWire.h"
#include <DallasTemperature.h>
#include <yasm.h>
#include <Streaming.h>
#include <RH_RF95.h>
#include "ArduinoLowPower.h"
#include <lmic.h>
#include <hal/hal.h>
#include "arduino_secrets.h" //this file should be placed in same folder as the sketch and contains your TTN session keys, see below for more details


// Firmware revision
String Firmw = "2.0";


#define MAX_SLEEP_ITERATIONS   LOGGING_FREQ_SECONDS / 10  // Number of times to sleep (for 10 seconds) before
// a sensor reading is taken and sent to the server.
// Don't change this but rather the variable "LOGGING_FREQ_SECONDS" above.

#define LumThreshold_LOW  5                 //Luminosity threshold to actuate door in the evenings
#define LumThreshold_HIGH 30                //Luminosity threshold to actuate door in the mornings

volatile bool ButtonUPPressed = false;
volatile bool ButtonDWNPressed = false;
volatile bool DoorMoving = false;
volatile bool DoorDWNStateForced = false;
volatile bool DoorUPStateForced = false;
volatile float measuredvlum = LumThreshold_HIGH;
volatile float measuredSolarlum = LumThreshold_HIGH;
volatile int sleepIterations = 0;

// Data wire is connected to input digital pin A4 of the Adafruit Feather 32u4 LoRa
#define ONE_WIRE_BUS_A A4

//Motorized door state machine
YASM Door;

//Door position
volatile double DoorWantedPos = 100.0;
volatile int DoorActualPos = 0;

//Door movements
#define DoorOPEN     1
#define DoorCLOSE    0
#define InContact    0  //endswitches state when in limit position

//Time required for the door to open + 20% or so. Serves as timeout in case endswitches don't work
const unsigned long DoorTimeConstant = 100000L; //100 sec
unsigned long DoorCycleStart = 0L;
unsigned long DoorCycleEnd = 0L;

String _endl = "\n";
String temp_str;
char temp[50];

//Digital inputs
#define STAT1  12  //Battery charging status
#define STAT2  11  //Battery done charging status
#define SwUP  10  //endswitch UP
#define SwDOWN  20  //endswitch DOWN
#define INTERLCK  20  //Main Door Interlock (not used yet)

//Motor controller pins
#define AIN1 A3
#define AIN2 A2
#define STBY A5

//Up and Down push buttons used to manually force open/close Hen's guillotine door
#define PUSH_BUTTON_UP    0 //INT2
#define PUSH_BUTTON_DOWN  1 //INT3

//Analog input pin to read the Battery level
#define VBATTPIN A1

//Analog input pin to read the ambient luminosity level
#define VLUMPIN A7

//Analog input pin to read the solar panel voltage (better option to measure the ambient luminosity level)
#define SOLPIN A0

// OneWire instance to communicate with the 4 DS18B20 temperature sensors
OneWire oneWire_A(ONE_WIRE_BUS_A);

// Pass our oneWire reference to Dallas Temperature library instance
DallasTemperature sensors_A(&oneWire_A);

//MAC Address of DS18b20 temperature sensor (!unique to every sensor!)
//DeviceAddress DS18b20_4 = { 0x28, 0x5F, 0x93, 0x03, 0x00, 0x00, 0x80, 0xE9 };//Slot1 temp
DeviceAddress DS18b20_4 = { 0x28, 0x9C, 0xD0, 0x00, 0x0C, 0x00, 0x00, 0x37 };//Slot1 temp
DeviceAddress DS18b20_3 = { 0x28, 0xB1, 0x7D, 0x00, 0x0C, 0x00, 0x00, 0x14 };//Slot2 temp
DeviceAddress DS18b20_1 = { 0x28, 0xCB, 0x32, 0xFF, 0x0B, 0x00, 0x00, 0x54 };//Slot3 temp
DeviceAddress DS18b20_2 = { 0x28, 0xD4, 0x68, 0x00, 0x0C, 0x00, 0x00, 0x92 };//Slot4 temp

//12bits (0,06°C) temperature sensors resolution
#define TEMPERATURE_RESOLUTION 12

// Data Packet to Send to TTN
// Bytes 0-1: Average temperature over two bytes
// Bytes 2-3: Slot1 temperature over two bytes
// Bytes 4-5: Slot2 temperature over two bytes
// Bytes 6-7: Slot3 temperature over two bytes
// Bytes 8-9: Slot4 temperature over two bytes
// Bytes 10-11: Luminosity voltage from varistor over two bytes
// Bytes 12-13: Luminosity voltage from solar panel output voltage over two bytes
// Bytes 14-15: Battery voltage over two bytes
// Bytes 16-17: digital inputs reading
static uint8_t loraData[20];
uint8_t DigInputs = 0;
static osjob_t sendjob;

// Pin mapping for Adafruit Feather M0 LoRa
// /!\ By default Adafruit Feather M0's pin 6 and DIO1 are not connected.
// Please ensure they are connected.
const lmic_pinmap lmic_pins = {
  .nss = 8,
  .rxtx = LMIC_UNUSED_PIN,
  .rst = 4,
  .dio = {3, 6, LMIC_UNUSED_PIN},
  .rxtx_rx_active = 0,
  .rssi_cal = 8,              // LBT cal for the Adafruit Feather M0 LoRa, in dB
  .spi_freq = 8000000,
};

//pinout of radio module for feather m0
#define RFM95_CS 8
#define RFM95_RST 4
#define RFM95_INT 3

// Singleton instance of the radio driver
// Will be used to put the radio module to deep sleep
RH_RF95 rf95(RFM95_CS, RFM95_INT);

//ready to go to sleep?
volatile bool DoorAtPosition = false;
volatile bool ReadyToSleep = false;
volatile bool JoinedOK = false;

//Interrupt handle if UP push button was pressed
void ButtonUPWake()
{
  detachInterrupt (digitalPinToInterrupt (PUSH_BUTTON_UP));      // stop LOW interrupt
  ButtonUPPressed = 1;
  ButtonDWNPressed = 0;
  DoorUPStateForced = 1;
  DoorDWNStateForced = 0;
}

//Interrupt handle if DOWN push button was pressed
void ButtonDWNWake()
{
  detachInterrupt (digitalPinToInterrupt (PUSH_BUTTON_DOWN));      // stop LOW interrupt
  ButtonDWNPressed = 1;
  ButtonUPPressed = 0;
  DoorDWNStateForced = 1;
  DoorUPStateForced = 0;
}

//Set individual bits of the DigInputs Byte
void writeBitmap(bool a, bool b, bool c, bool d, bool e, bool f, bool g, bool h)
{
  // LSB first
  DigInputs = 0;
  DigInputs |= (a & 1) << 7;
  DigInputs |= (b & 1) << 6;
  DigInputs |= (c & 1) << 5;
  DigInputs |= (d & 1) << 4;
  DigInputs |= (e & 1) << 3;
  DigInputs |= (f & 1) << 2;
  DigInputs |= (g & 1) << 1;
  DigInputs |= (h & 1) << 0;
}

void printHex2(unsigned v) {
  v &= 0xff;
  if (v < 16)
    Serial.print('0');
  Serial.print(v, HEX);
}
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
void loop()
{

  // we call the LMIC's runloop processor. This will cause things to happen based on events and time. One
  // of the things that will happen is callbacks for transmission complete or received messages. We also
  // use this loop to queue periodic data transmissions.  You can put other things here in the `loop()` routine,
  // but beware that LoRaWAN timing is pretty tight, so if you do more than a few milliseconds of work, you
  // will want to call `os_runloop_once()` every so often, to keep the radio running.
  os_runloop_once();

  //if Button UP interrupt has fired
  if (ButtonUPPressed)
  {
    //Door setpoint at 100% (open)
    DoorWantedPos = 100.0;

    //Serial.println(counter);
    ButtonUPPressed = 0;
    ButtonDWNPressed = 0;

    // blink LED 
    digitalWrite(LED_BUILTIN, HIGH);
    delay(100);
    digitalWrite(LED_BUILTIN, LOW);

    // Allow wake up pin to trigger interrupt on low.
    LowPower.attachInterruptWakeup(digitalPinToInterrupt(PUSH_BUTTON_UP), ButtonUPWake, LOW);
  }

  //if Button DOWN interrupt has fired.
  if (ButtonDWNPressed)
  {
    //Door setpoint at 0% (closed)
    DoorWantedPos = 0.0;

    //Serial.println(counter);
    ButtonDWNPressed = 0;
    ButtonUPPressed = 0;

    // blink LED 
    digitalWrite(LED_BUILTIN, HIGH);
    delay(100);
    digitalWrite(LED_BUILTIN, LOW);

    // Allow wake up pin to trigger interrupt on low.
    LowPower.attachInterruptWakeup(digitalPinToInterrupt(PUSH_BUTTON_DOWN), ButtonDWNWake, LOW);
  }

  //update Door state engine
  Door.run();

  //Open door at sunrise and close it at sunset, based on an ambient luminosity threshold
  if ((!DoorDWNStateForced) && (measuredSolarlum > LumThreshold_HIGH)) //Door is closed and luminosity > LumThreshold_HIGH% ->open door
  {
    DoorWantedPos = 100.0;
    DoorUPStateForced = 0;
  }
  else if ((!DoorUPStateForced) && (measuredSolarlum < LumThreshold_LOW)) //Door is open and luminosity < LumThreshold_LOW% ->close door
  {
    DoorWantedPos = 0.0;
    DoorDWNStateForced = 0;
  }

  if (sleepIterations >= MAX_SLEEP_ITERATIONS)
  {
#ifdef DEBUG
    Serial.begin(115200);
    while (! Serial);
    delay(1000);
    Serial.println("Just woke up!");
#endif
    // Reset the number of sleep iterations.
    sleepIterations = 0;

    //wake radio module and send lora message
    Serial.println("LoRa radio init OK!");

    //send sensors data over LoRaWan on port 3
    LoraPublish(&sendjob, 3);
  }

#ifdef SLEEP
  // Go to sleep if door is at desired position, sensor has successfully joined LoRaWan network and nothing else to do
  if (((int)DoorWantedPos == DoorActualPos) && JoinedOK && ReadyToSleep)
  {
    // Show we're asleep
    digitalWrite(LED_BUILTIN, LOW);

    //put radio module to deep sleep
    rf95.sleep();

    //put controller to deep sleep
    LowPower.deepSleep(10000);  // Sleep for 10 seconds.

    //We are awake
//#ifdef DEBUG
    digitalWrite(LED_BUILTIN, HIGH); // Show we're not asleep anymore
//#endif
    sleepIterations += 1;

  }
#endif
 // Door.next(Door_wait);
}

void LoraPublish(osjob_t* j, unsigned char port)
{
  ReadyToSleep = false;

  // Check if there is not a current TX/RX job running
  if (LMIC.opmode & OP_TXRXPEND) {
    Serial.println(F("OP_TXRXPEND, not sending"));
  }
  else
  {
    //port 3 is used to send sensors data at regular intervals
    if (port == 3)
    {
      sensors_A.requestTemperatures();
      float S1 = sensors_A.getTempC(DS18b20_1);
      float S2 = sensors_A.getTempC(DS18b20_2);
      float S3 = sensors_A.getTempC(DS18b20_3);
      float S4 = sensors_A.getTempC(DS18b20_4);
      float tm = (S1 + S2 + S3 + S4) / 4.0;

      // scale to -1 to 1 range
      S1 /= 100.0;
      S2 /= 100.0;
      S3 /= 100.0;
      S4 /= 100.0;
      tm /= 100.0;

      // float -> int
      // note: this uses the sflt16 datum (https://github.com/mcci-catena/arduino-lmic#sflt16)
      uint16_t payloadS1 = LMIC_f2sflt16(S1);
      uint16_t payloadS2 = LMIC_f2sflt16(S2);
      uint16_t payloadS3 = LMIC_f2sflt16(S3);
      uint16_t payloadS4 = LMIC_f2sflt16(S4);
      uint16_t payloadtm = LMIC_f2sflt16(tm);

      //Read luminosity level
      measuredvlum = analogRead(VLUMPIN);
      measuredvlum /= 1024; // convert to 0-1 range
      // float -> int
      // note: this uses the sflt16 datum (https://github.com/mcci-catena/arduino-lmic#sflt16)
      uint16_t payloadlum = LMIC_f2sflt16(measuredvlum);

      //Read solar panel luminosity level
      measuredSolarlum = analogRead(SOLPIN);
      measuredSolarlum /= 1024; // convert to 0-1 range
      float SolLum = measuredSolarlum;
      measuredSolarlum *= 100.0; // convert to % -> required to check for open/close motorized door in loop()
      // float -> int
      // note: this uses the sflt16 datum (https://github.com/mcci-catena/arduino-lmic#sflt16)
      uint16_t payloadsolarlum = LMIC_f2sflt16(SolLum);

      //Read battery level
      float measuredbatt = analogRead(VBATTPIN);
      measuredbatt *= 6.6;  // 100% = 3.3*2V because of voltage divider
      measuredbatt /= 1024; // convert to %
      measuredbatt /= 100.0; // scale to 0-1 range
      // float -> int
      // note: this uses the sflt16 datum (https://github.com/mcci-catena/arduino-lmic#sflt16)
      uint16_t payloadbatt = LMIC_f2sflt16(measuredbatt);

      //Read the Digital inputs states and record them into a Byte to be sent in the message payload
      writeBitmap(false, digitalRead(INTERLCK), digitalRead(SwDOWN), digitalRead(SwUP), digitalRead(STAT2), digitalRead(STAT1), ButtonUPPressed, ButtonDWNPressed);

#ifdef DEBUG
      String msg = F("VBat: ");
      msg += measuredbatt;
      msg += F("V\t");
      msg += F("Lum: ");
      msg += measuredvlum;
      msg += F("%\t");
      msg += F("SoLum: ");
      msg += SolLum;
      msg += F("%\t");
      msg += F("Avg Temp: ");
      msg += tm;
      msg += F("°C\t");
      msg += F("S1 Temp: ");
      msg += S1;
      msg += F("°C\t");
      msg += F("S2 Temp: ");
      msg += S2;
      msg += F("°C\t");
      msg += F("S3 Temp: ");
      msg += S3;
      msg += F("°C\t");
      msg += F("S4 Temp: ");
      msg += S4;
      msg += F("°C\t");
      msg += F("DigInputs: ");
      msg += DigInputs;

      DEBUG_PRINT(msg);
#endif

      // encode int as bytes
      loraData[0] = lowByte(payloadtm);
      loraData[1] = highByte(payloadtm);

      loraData[2] = lowByte(payloadS1);
      loraData[3] = highByte(payloadS1);

      loraData[4] = lowByte(payloadS2);
      loraData[5] = highByte(payloadS2);

      loraData[6] = lowByte(payloadS3);
      loraData[7] = highByte(payloadS3);

      loraData[8] = lowByte(payloadS4);
      loraData[9] = highByte(payloadS4);

      loraData[10] = lowByte(payloadlum);
      loraData[11] = highByte(payloadlum);

      loraData[12] = lowByte(payloadsolarlum);
      loraData[13] = highByte(payloadsolarlum);

      loraData[14] = lowByte(payloadbatt);
      loraData[15] = highByte(payloadbatt);

      loraData[16] = highByte(0);
      loraData[17] = lowByte(DigInputs);
    }
    else if (port == 4) //port 4 is used to send door opening/closing progress at short intervals only when door is moving
    {
      //Read the Digital inputs states and record them into a Byte to be sent in the message payload
      writeBitmap(false, digitalRead(INTERLCK), digitalRead(SwDOWN), digitalRead(SwUP), digitalRead(STAT2), digitalRead(STAT1), ButtonUPPressed, ButtonDWNPressed);

#ifdef DEBUG
      String msg = F("Door wanted pos: ");
      msg += DoorWantedPos;
      msg += F("%");
      msg += F(" - Door actual pos: ");
      msg += DoorActualPos;
      msg += F("%\t");
      msg += F("DigInputs: ");
      msg += DigInputs;

      DEBUG_PRINT(msg);
#endif

      //convert float to int
      int iDoorWantedPos = round(DoorWantedPos);

      // encode int as bytes
      loraData[0] = highByte(iDoorWantedPos);
      loraData[1] = lowByte(iDoorWantedPos);

      loraData[2] = highByte(DoorActualPos);
      loraData[3] = lowByte(DoorActualPos);

      loraData[4] = highByte(0);
      loraData[5] = lowByte(DigInputs);
    }

    DEBUG_PRINT("Sending LoRa Data...");

    // prepare upstream data transmission at the next possible time.
    // transmit on "port" (the first parameter); you can use any value from 1 to 223 (others are reserved).
    // don't request an ack (the last parameter, if not zero, requests an ack from the network).
    // Remember, acks consume a lot of network resources; don't ask for an ack unless you really need it.
    LMIC_setTxData2(port, loraData, sizeof(loraData) - 1, 0);

    // blink LED to indicate packet sent
    digitalWrite(LED_BUILTIN, HIGH);
    delay(100);
    digitalWrite(LED_BUILTIN, LOW);
  }
}
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

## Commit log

2020-04-26 Interrupts now working as intended
2020-04-27 added schematics
    [HenHouse.fzz]
2020-05-04 Create HenHouse schematics.png
2020-05-05 Update HenHouse schematics.png
2020-05-20 more docs
    [LDR bias resistor selection.xlsx]
2021-12-06 Project ported to Adafruit Feather M0 board and LoraWan LMIC library
    [HenHouse.fzz, LDR bias resistor selection.xlsx]
